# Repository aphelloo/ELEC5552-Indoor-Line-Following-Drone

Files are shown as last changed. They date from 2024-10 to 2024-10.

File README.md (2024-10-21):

# ELEC5552 Electrical Design Project Part 2 - Indoor Line Following Drone
<p align="center">
Project Overview
</p>

## Overview
The UWA Aviation Labs (UWAAL) consists of staff and students dedicated to developing advanced drone systems for various applications. UWAAL is currently working on an indoor drone system designed to perform autonomous remote safety inspections within the Australian National Fabrication Facility (ANFF) laboratories. Given the confined space and lack of GPS signal for navigation, the drone will be programmed to follow a predefined path marked by a line on the floor and hover at specific locations. Additionally, the drone will be equipped with obstacle avoidance capabilities to ensure safe and efficient operations during the inspection process.

## Repository Structure

| Section | Description |
| --- | --- |
| 3D CAD Design | For 3D Printed Shroud Design |
| Calculations | Calculations for component sizing |
| Code | Includes code-flow diagrams and programming files |
| Construction and Risks | Documentation on construction procedures and risk assessments associated with the project |
| Manual | Instructions for operation, safety and maintenance |
| Schematics | Schematics for drone, outlining the various connections |

## Required Applications
### On Laptop
* Betaflight Configurator
* Arduino IDE
* Raspberry Pi Imager
### On Phone
* Raspcontroller

## Acknowledgements
This project is made possible by contributions and feedback from the open-source hardware community, with support from ELEC5552 course staff and students.

## Licence
The CERN Open Hardware Licence Version 2 - Permissive (CERN-OHL-P) was chosen for its commitment to transparency and collaboration, allowing unrestricted use, modification, and distribution of the hardware designs and documentation. This license facilitates innovation and sharing within the community, ensuring that all adaptations and improvements remain openly accessible under the same terms. 

## Contributors
* Shraddha Domdala 
* Sharla Greyvenstein 
* Kate Miller 
* Ankona Pahari
* Anusree Rejukumar
* Thomas Robertson

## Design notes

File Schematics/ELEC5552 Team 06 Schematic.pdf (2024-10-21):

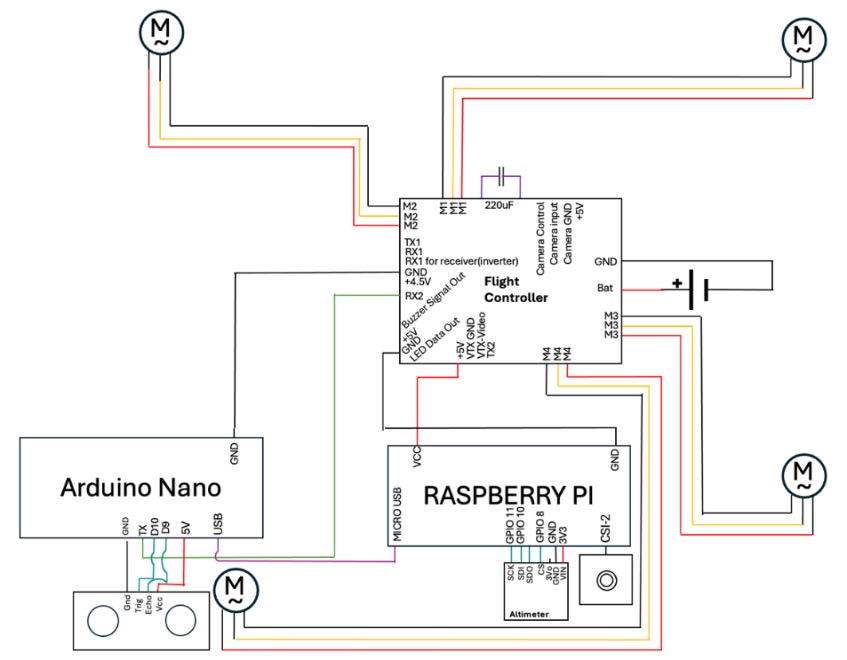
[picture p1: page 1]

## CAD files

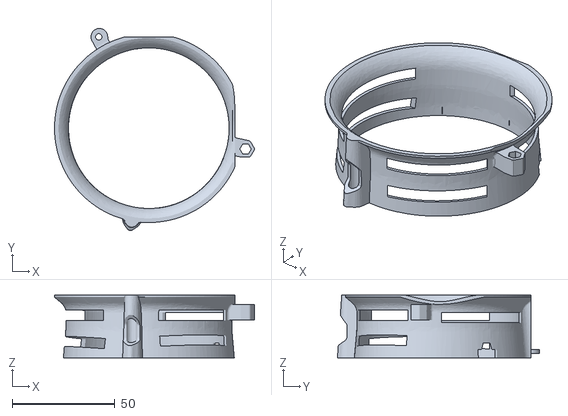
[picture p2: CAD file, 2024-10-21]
3D CAD Design/Front Right Shroud.stl
97.3 x 98.4 x 30.5

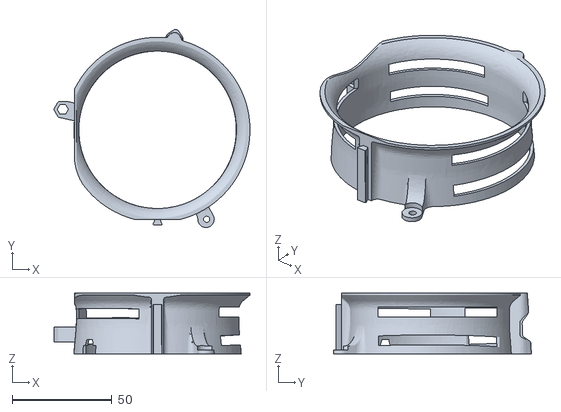
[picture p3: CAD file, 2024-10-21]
3D CAD Design/Rear Left Shroud.stl
98.3 x 99.3 x 30.5

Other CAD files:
3D CAD Design/Front Left Shroud.stl
3D CAD Design/Rear Right Shroud.stl

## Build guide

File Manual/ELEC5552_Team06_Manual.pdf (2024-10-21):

## Indoor Line Following Drone Project Team 06

Author(s)
Shraddha Domdala (23695285) Sharla Greyvenstein (22969519) Kate Miller (22965308)
Ankona Pahari (22903372)
Anusree Rejukumar (23943712) Thomas Robertson (23137408)

## Manual

## Volume 1

Project Partners: UWA Aviation Labs, Australian National Fabrication Facility (ANFF)

UWA Supervisor: John Dell

Team Number: 6

Group Meeting Day and Time: Tuesday 4pm

Word Count: 2258

### Version 2.0

## Revision History

Date | Version | Description | Author
10th September 2024 | 1.0 | Document has been initiated. | All
20th September 2024 | 2.0 | Edited Version | S. Greyvenstein

Contents Page

1. Safety

4
1.1 General Safety Warnings

4
1.2 Pre -Flight Safety Checklist

4
1.3 Operational Safety

4
1.4 Post Flight Safety

5
1.5 Emergency Action

5
1.6 Handling Hazardous Materials

5
1.7 Maintenance Safety

5

2. Operation

5
2.1 Required Prior to First Use

5
2.2 Operational Steps

6

3. Maintenance

7
3.1 Component Maintenance

7
3.2 Connection Maintenance

8

## Indoor Line-Following Drone Operation and Maintenance Manual

## 1. Safety

### 1.1 General Safety Warnings

- Prior to operating the drone, ensure you have thoroughly read and understood this manual. This will reduce the risks of accidents and potential harm to the user, bystanders, the surroundings, and the drone itself. Retain this manual for future reference.
- Indoor-use only: This drone has been designed, built, and coded for indoor operation. Use of the drone in an outdoor environment is beyond the specifications of this drone. Issues that may arise include but are not limited to; signal loss, unstable flight due to wind, dust, dirt, or moisture accumulation in components leading to potential malfunctions, overheating, or permanent damage.
- Avoid proximity to heat sources: Keep the drone away from heat sources as exposure to high temperatures can damage components or cause overheating.
- Avoid contact with water: Ensure the drone is kept away from water and other liquids. Exposure to moisture can lead to malfunctions and increase the risk of a crash.
- Do not touch operational drone: Whilst the drone is in flight, do not touch the under any circumstances
- 14+: This drone is intended for use by persons aged 14 years or older.
- Keep drone within sight: Do not allow drone to fly out of visible range.

### 1.2 Pre-Flight Safety Checklist

- Battery Inspection: Prior to each flight, inspect the drone battery. Ensure battery is fully charged and securely connected. Do not use a damaged, swollen, or leaking battery
- Component functionality tests: Run test codes for the flight controllers, microcontrollers, and sensors to confirm correct functionality.
- E-Stop operation validations: Verify the E-stop is functioning correctly and is accessible during flight. This enables immediate shutdown in the case of malfunction or unforeseen obstacles.
- Inspect motor windings: Verify that motor windings are clear of debris and appear undamaged.
- Inspect propellers: Verify that propellers are undamaged and that they are firmly attached to the motor shafts.

### 1.3 Operational Safety

- Ensure flight area is free from unnecessary bystanders: Avoid flying drone in area high crowded with bystanders.
- Maintain a safe distance from operational drone: Establish a safe distanced between the operator and bystanders, and the drone. Do not operate the drone near one’s face or eyes.

### 1.4 Post Flight Safety

- Safely turn off the drone: Upon flight completion (landed drone and stationary propellers) disconnect the battery.
- Damage inspection: After the drone has been safety depowered, inspect the drone for damage. Do not operate the drone if any part appears damaged or malfunctioning.
- Safe battery storage: Store the LiPo battery in an appropriately rated LiPo fireproof bag. Keep bag in a cool, dry location.
- Safe battery charging: Battery charging must be done under supervision and in a location out of reach of children. Allow battery to cool after use prior to charging. Do not charge a swollen or leaking battery.

### 1.5 Emergency Action

- Fire: If smoke or fire is present, do not handle the drone. Use a Carbon Dioxide Fire Extinguisher to extinguish flames.
- Crash response: In case of drone crash mid-flight, turn off the drone by disconnecting the battery prior to inspecting the drone for damage.

### 1.6 Handling Hazardous Materials

- Safe battery disposal: Do not dispose of the battery in curb side rubbish. Review your local disposal laws.
- Avoid contact with leaking battery: If battery leakage occurs, avoid contact with eyes or skin. If contact transpires, thoroughly wash exposed area with water and seek medical attention immediately.

### 1.7 Maintenance Safety

- Disconnect battery during maintenance: If maintenance works are to be performed on the drone, ensure battery is disconnected.
- Use proper tools: When changing or modifying drone parts, use only appropriate equipment and follow the manufacturer's instructions.

## 2. Operation

### 2.1 Required Prior to First Use

- Phone/Tablet with IOS or android access: To interact with the drone the user must download Raspcontroller, a free app which allows the user to remotely change GPIO pins.
- Stable Wi-Fi/Hotspot: To communicate with the Raspberry Pi, it must be connected to a local Wi-Fi
- MicroUSB Reader: In order for the Pi to operate in headless mode, the local Wi-Fi settings must be added to the bootup code. This is covered in Section 2.2.
- Line requirements: The line must be 8cm wide and be highly contrasting with the ground which itself cannot have complex patterns as this risks confusing the drone.

### 2.2 Operational Steps

1. Connecting to new Wi-Fi: For first use or when Wi-Fi settings have changed, complete the following steps.
a. Connect Raspberry Pi’s SD card into a SD card reader
b. Create a file called wpa_supplicant.conf
c. Put the following code into the wpa_supplicant.conf file. Ensure the County, SSID and PSK values are for your Wi-Fi settings.

country=AU
ctrl_interface=DIR=/var/run/wpa_supplicant GROUP=netdev update_config=1
network={
ssid="Your_SSID"
psk="Your_Password"
}
d. Insert SD Card into Raspberry Pi
2. Connect battery: The 2S battery must be firmly connected to the flight controller via the power cables located at the back of the drone. Care must be taken in ensuring the correct polarity is followed (black – black and red – red).
3. Ensure Power is reaching all components: Once the battery is connected, ensure the lights on the flight controller, Arduino, and Raspberry Pi have been activated. If there are any issues please refer to 1.d in Maintenance.
4. Wait for the Raspberry Pi light to stop flashing: Once the light has stopped flashing the Raspberry Pi has completed booting meaning the user will be able to connect. If this is the first time connecting the Raspberry Pi, please move to step 5 if not skip to step 6
5. First time Connection via Raspcontroller: In the Rasp controller app press the plus button. This will allow the user to enter information to be able to connect to the drone. Please enter the following values:
Device name: | drone
Host/IP Address: | drone.local
SSH Port: | 22
Timeout (sec): | 15
Username: | drone
Authentication: | Password
Password: | drone

Once these values have been entered press connection test.
6. Connection via Raspcontroller continued: Once connected this app can allow the user to check the camera, monitor CPU and RAM functionality, and remotely control the GPIO pins.
7. Connection via Raspcontroller continued – Remote GPIO: Once on GPIO control, the user must add GPIO5, GPIO19, GPIO21, GPIO26. Once enabled ensure they are all set to OUT and 0.
8. GPIO Functionality: The following commands are linked to GPIO pins:

GPIO5: | Arming Drone
GPIO19: | Hovering Mode
GPIO21: | Line Following Mode
GPIO26: | E-stop
9. Arming the Drone: The user must set GPIO5 to 1 to arm the drone – without this pin actived the drone will not function.
10. Launching the Drone: Following all safety instructions and keeping a safe distance away, setting GPIO19 to 1 will launch the drone to a stable height. When in this mode the drone will hover at a specific height and await further instructions.
11. Line Following: Setting GPIO21 to 1 will enable the line following mode. Ensure the drone is able to see the path through the check camera functionality on Raspcontroller. If no line is detected the drone will not leave hovering mode. Once line following has begun no more direct inputs are needed. For Line functionality, if the user requires the drone to stop at a particular place on the route, please use a perpendicular line. This will cause the drone to hold for 30s.
12. Emergency situations: If at any time the drone is operating in an unplanned manner that can be dangerous or if the drone needs to urgently stopped, set GPIO26 to 1. This will enable the drone’s failsafe mode causing it to land where it is.
13. Notes: Users should be aware that if the drone leaves Wi-Fi range for 30s the failsafe mode will also active.

## 3. Maintenance

### 3.1 Component Maintenance

a. Propeller: Propellers need to be regularly inspected before every flight to ensure that the propellers are not misshaped, discoloured, or fractured as these indicate that the propeller is worn/ old and needs replacement. Propellers should otherwise be replaced annually or after flying over 300 hours. Propellers should also be wiped down to clean off any foreign materials using a soft, dry cloth.
b. Motor: Motors should be regularly cleaned to remove dust and debris using a soft brush or cloth. A lubricant can be applied to the shaft and bearings to reduce noise and friction. Motor windings should be rotated by hand to check for blockages or rubbing prior to usage. Motor windings can also be inspected for any visual deformations. Do not do any powered testing of the motor if blockage, rubbing, or deformation is discovered. Instead, clean or replace where necessary. If not discovered, briefly power the motor and listen for any unusual sounds as these may indicate issues with the motor bearings. To extend motor longevity, avoid overloading as this puts additional strain on the motors.
c. Camera: Inspect the camera lense for any scratched, smudges, or foreign materials and ensure that the camera is firmly positioned before every flight. The camera lense can be wiped using a dust-free or microfibre cloth. If scratches are interfering with image-processing accuracy, camera replacement is necessary.
d. Battery: To guarantee optimal drone battery performance and longevity, inspect the battery on a regular basis for any physical damage, swelling, or leaks. If any of these are discovered, replace and dispose of the damaged battery safely according to local rules. Use a balance charger to equally charge all cells, preventing overcharging and extending battery life. Charge the battery to 50-60% capacity before storing it in a cool, dry location away from direct sunlight or harsh temperatures. If the battery is not in frequent use, cycle it every 1-2 months and avoid discharging it below 20% to prevent damage.
e. Frame: Inspect the frame on a regular basis for visible cracks, particularly after hard landings or crashes, and repair any damaged components to maintain structural integrity. Periodically check and tighten screws, especially those near motor mounts and frame connections, as vibrations can cause loosening over time. Clean the frame with compressed air or a soft brush to remove dirt, dust, and debris, paying special attention to vital places like motor mounts and gimbals to maintain smooth operation and avoid performance difficulties.
f. Frame arms: Inspect the frame arms on a regular basis for signs of warping, bending, or cracking, and replace any damaged arms as soon as possible. If weak areas or minor cracks emerge, consider strengthening them with epoxy or carbon fiber tape, however replacement is typically the best solution. Check that motor mounts are tightly attached, as loose screws might cause vibrations and performance concerns. Also, ensure that the propellers are balanced, since uneven propellers can put unnecessary strain on the frame arms, potentially causing damage over time.
g. Shrouds: As the shrouds are 3D printed, inspect them before and after each flight for cracks, deformation, or wear, especially following impacts. Clean them regularly to remove debris that could affect aerodynamics. Replace any damaged shrouds immediately using the same 3D print shroud layout to maintain consistency. When replacing, verify the size, and if needed, smooth the edges with sandpaper to ensure a proper fit. Store the drone in a dry, cool place to prevent unnecessary wear or pressure on the shrouds.

### 3.2 Connection Maintenance

a. Screw condition: Loose or worn screws can lead to mechanical failures or vibrations that reduce the drone’s overall performance. After every flight, inspect all screws for tightness, especially those securing the motors, and other moving parts. Vibration during flight can cause screws to loosen over time. Replace screws that show signs of wear, such as stripped threads or rust. Corrosion can compromise structural integrity and make it difficult to tighten or remove screws when necessary. When replacing screws, ensure they are not over-tightened, especially those securing the motors, as excessive force can damage the motor windings and compromise motor functionality. Apply thread locker solution (a mild one) to screws that are prone to loosening. This will ensure that they stay secure during flights while still being removable for maintenance.
b. Soldering condition: Soldered connections are crucial for maintaining electrical continuity in the power supply. Regularly inspect solder joints for cracks, cold joints, or oxidation, as weak points can lead to power loss or signal disruption. If any joint shows signs of wear, re-solder it immediately, taking proper precautions. When re-soldering, ensure no two connections are shorted and use a multimeter to verify continuity and detect any disconnections. Ensure cables and connectors are well-supported to avoid strain that could damage solder joints, especially those on the flight controller. During routine maintenance, handle the drone with care to prevent accidental pulling on these connections.
c. Cable condition: The condition of cables are crucial for power delivery and control signals. Ensure cables are neatly routed and secured with cable ties to prevent snagging and tangling, which can lead to disconnections or damage. Regularly inspect cables for fraying, exposed wires, or insulation damage, and replace any damaged cables immediately to avoid short circuits. Ensure that no wires cross the motor and propeller area to prevent cuts or entanglements, and handle the cable connection carefully especially the battery cable. Verify that all connectors are securely attached and free of corrosion or debris to maintain electrical continuity.

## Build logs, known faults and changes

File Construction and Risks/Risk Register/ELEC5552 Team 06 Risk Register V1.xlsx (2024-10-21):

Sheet: Risk Register
 | PROJECT RISK REGISTER
 | A risk is any factor, event or influence that threatens the successful completion of the project.
RISK DESCRIPTION |  | POTENTIAL IMPACT | RISK ASSESSMENT (Pre-mitigation) |  |  | RISK TREATMENT / MITIGATION | RISK ASSESSMENT (Post-mitigation) |  |  | RESPONSIBILITY
 |  |  | Consequence | Likelihood | Risk Rating- from risk matrix |  | Consequence | Likelihood | Risk Rating- from risk matrix
NO. | Project Scope
1 | Inadequate identification of in scope tasks | Not all aspects of scope was addressed in design | Major | Likely | E | Ask project partner clear technical clarifications | Major | Rare | M | All members- Identify TQs. Project Laison Manager- Submit TQs and attend info sessions.
2 | Inadequate identification of out of scope tasks | Time and effort put towards an aspect of the project that is irrelevant/ not under our control | Minor | Likely | H | Ask project partner clear technical clarifications | Minor | Unlikely | L | All members- Identify TQs. Project Laison Manager- Submit TQs and attend info sessions.
3 | Incorrect interpretation of scope | May inadvertantly go against a requirement | Major | Possible | E | Ask project partner clear technical clarifications in person when TQ response is received and a vague response is identified. Look at TQ responses from other groups. | Major | Rare | M | All members- Identify if response is unclear. Project Client Laison Manager - Raise questions to Project Partner.
4 | Scope creep | Change in scope was not identified or addressed, resulting in design proposed being based on out of date requirements | Moderate | Likely | H | Actively track requirements, updating when TQ responses are received and notifying all members if any changes to scope was made. | Moderate | Unlikely | M | Project Admin
 | Project Quality
5 | Project Team has limited experience with communication technologies | Limited knowledge means a lack of clarifty of complexity, impacting the quality of the design that can be delivered. | Minor | Possible | M | Research communication basics and components prior to starting design process | Minor | Unlikely | L | All members
6 | Project Team has limited experience with PCB design work | Limited capability to design PCBs impacts the quality of the design tha can be delivered. | Minor | Possible | M | Research PCB designs of revelant past projects to build knowledge of PCB design components. | Minor | Unlikely | L | All members
7 | Unclear level of quality demanded by project partner | May not deliver a design/ report that satisfies the expected standards quality | Minor | Possible | M | Be attentive to the rubrics of each area | Minor | Unlikely | L | All members
8 | Disagreements of individual expectation of quality | Members deliver sections with differing levels of quality, causing inconsistency in report flow or dissatisfaction among member regarding value of contribution | Minor | Likely | H | Check up with each individual's progress consistently to make sure disagreements/ dissatisfaction is not raise in the later half of the project | Minor | Unlikely | L | All members
9 | Being unable to find component meeting requirements | Unable to satisfy all requirements | Moderate | Possible | H | Be sure to look into multiple sources. If none is found meeting all requirements, pick a component that meets the essentials | Minor | Possible | M | All members
10 | Inadequate prioritising | May result in higher priority tasks being neglected, hence impacting their quality | Minor | Possible | M | Members must pay attention to rubric and course schedule to identify high priority tasks/ sections | Minor | Unlikely | L | All members
 | Project Schedule
11 | Unrealistic deadlines | Unrealistic deadlines may result in sections either being rushed and completed to a below-desired standard, or there being a knock on effect of tasks completed behind schedule | Moderate | Likely | H | Creation of a Gantt chart that allocates a realistic amount of time, accounting for how many tasks are expected to be completed concurrently and their priority | Minor | Possible | M | Project Controller
12 | Delay in prerequisite tasks | Delay in tasks that need to be completed before others can be started results in delay of progression of project | Moderate | Possible | H | Allocate enough members to complete prerequisite tasks to prevent delay | Minor | Unlikely | L | All members
13 | Unidentified tasks during schedule creation | Missed opportunity to do the tasks during the optimal time, causing delay in progression of project | Minor | Possible | M | Disect all rubrics and guides to identify what components are expected to be covered | Minor | Unlikely | L | All members
14 | Higher external priorities | Members having higher external may mean some individuals become unavailable at inopportune times, causing delay in their contribution or communication | Moderate | Likely | H | All members must give warning if they foresee a period of time during which they will be unavailable. Members must complete their contribution prior to becoming unavailable. | Minor | Possible | M | All members
15 | Change in submission dates | Reduces time in which project can be completed, resulting in requirement to review project schedule to prevent missing submission date | Moderate | Rare | M | All members must regularly attend to updates made on LMS or during lecture/ info sessions and notify other members. Gantt chart should also be designed such that tasks are completed prior to the submission dates. | Minor | Rare | L | All members - Check LMS, lectures, info session announcements Project Controller- Create optimistic Gantt chart
16 | Conflicting idea proposal | Conflicting idea proposals require member to spend more time to investigate each option to determine best option | Minor | Possible | M | Members making proposals should already have facts backing their proposal to allow other members to come to the decision without requiring more research, hence time. | Insignificant | Possible | L | All members
17 | Delayed TQ reponses | May delay ability to move on to next tasks/ make informed decisions | Minor | Likely | H | Identify tasks that can be worked on without the most up to date information. | Insignificant | Likely | M | All members
18 | Missed TQ submission deadline | Delays ability to move on to next tasks/ make informed decisions as clarification questions are unable to be answered until next info session | Moderate | Possible | H | All members must upload their TQs to the register a day prior to the submission date. TQ submissions must be done the night before the submission date. Upcoming submission dates will be raised. | Moderate | Unlikely | M | All members - Upload TQs Project Controller- Remind Project Client Laison Manager of submission deadline. Project Client Laison Manager: Submit TQs prior to deadline.
19 | Missed information session | Delays ability to move on to next tasks/ make informed decisions as clarification questions are unable to be answered until next TQ submission date | Minor | Possible | M | Discuss among member such that at least one member must attend the session live. TQ submission should also be comprehensive such that only clarification of TQs are needed. | Minor | Rare | L | All members
20 | Mental stress | Stress may incur over the course of the project, resulting in members getting overwhelmed and unable to work efficiently, slowing down progress | Minor | Likely | H | Create a Gantt chart that allocates adequate time and allocate tasks to prevent overloadin a particular individual. | Minor | Unlikely | L | All members
21 | Poor design | May result in requirement to redesign, meaning more time spent on research and report rewrite and re-running simulations. | Major | Possible | E | All members must throroughly research their topic. Raise TQs if clarification is required. | Moderate | Unlikely | M | All members
22 | Missed submission date | Unable to complete all tasks to meet project deadline, resulting in lost marks every day it's late | Moderate | Possible | H | All members must be aware of course schedule. Upcoming submission dates will be raised. | Moderate | Unlikely | M | All members- Be aware of course schedule. Project Controller- Remind members of upcoming submission dates.
 | Project Cost
23 | Project is over budget | Project components may be overbudget as a result of meeting requirements, resulting in exceeding the budget limit | Moderate | Possible | H | Select components by taking cost into account. | Moderate | Unlikely | M | All members
24 | Lack of local resources | Lack of local resources means reliance on imported goods, raising risks of being overbudget as there are import/ shipping fees and currency conversion. | Minor | Likely | H | Ask other groups about sources (not specific components) | Minor | Unlikely | L | All members
25 | Lack of access to open-source resources for simulation/ modelling | Lack of open-source resources means reliance on resources that require obtaining a license and paying fees | Minor | Possible | M | Enquire into possible resources through TQs. | Minor | Unlikely | L | All members
 | Project Stakeholders
26 | Lack of communication management | Lack of communication management could damage relationship with stakeholder, reducing their willingness to contribute/ collaborate. | Moderate | Possible | H | Be clear and concise when asking clarifications (making sure questions are relevant) from Project Partner. | Minor | Unlikely | L | All members.
27 | Lack of communication among project team | Confusion about task allocations, deadline and/or design hinders effective completion of design project | Moderate | Possible | H | Be clear and concise when allocating tasks and merging individual contributions. | Minor | Possible | M | All members
28 | Unidentified stakeholder | Stakeholder's requirements are unaddressed | Moderate | Possible | H | Ask Dilusha clarification questions about specific stakeholders | Minor | Unlikely | L | All members
29 | Unclear role of stakeholder | Unclear identification of how stakeholder affects project may deterriorate relationship with them as they are not properly handled | Minor | Possible | M | Ask Dilusha clarification questions about specific stakeholders | Minor | Unlikely | L | All members
30 | Lack of integration of feedback | Feedback is not address in design, leading to neglecting the stakeholder. | Moderate | Possible | H | Regularly attend to the registries and notify members if changes were made. | Moderate | Unlikely | M | All members
 | Risks in Design
31 | Propeller interference | Propeller coming in contact with objects, causing damage or potentially breakage of the propeller. | Major | Likely | E | Propeller guards of shrouds to protect the propellers | Major | Unlikely | M | All members, end users
32 | Component Failure | Components in the drone (motors, propellers, battery, sensors, flight controller, ESC, communication modules, MCUs, or power distribution system) could fail due to mechanical stress, overheating, electrical faults, or poor handling. | Major | Likely | E | Regular maintenance and inspections should be performed on all critical parts to detect wear and potential issues early. | Moderate | Unlikely | M | All members, end users
33 | Communication Loss | There could be communication delays or loss of signal between the Raspberry Pi and the Arduino Nano, causing delays in executing commands. Communication loss may also interfere with E-stop functionality. | Moderate | Possible | H | Use reliable communication protocols and include error-checking mechanisms to ensure commands are executed properly. | Minor | Unlikely | L | All members, end users
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

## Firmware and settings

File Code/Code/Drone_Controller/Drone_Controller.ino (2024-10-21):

#include "global.h"
#include "SER.h"
//Choose either pin 2 or pin 3 because they are interrupt pins. On other boards you can use any pin that has an interrupt
#define OUTPUT_PIN 3 
#define RC_CHANNEL_MIN 990
#define RC_CHANNEL_MAX 2010

#define SBUS_MIN_OFFSET 173
#define SBUS_MID_OFFSET 992
#define SBUS_MAX_OFFSET 1811
#define SBUS_CHANNEL_NUMBER 16
#define SBUS_PACKET_LENGTH 25
#define SBUS_FRAME_HEADER 0x0f
#define SBUS_FRAME_FOOTER 0x00
#define SBUS_FRAME_FOOTER_V2 0x04
#define SBUS_STATE_FAILSAFE 0x08
#define SBUS_STATE_SIGNALLOSS 0x04
#define SBUS_UPDATE_RATE 15 //ms
int ch0 = 1500 , ch1 = 1500 , ch2 = 900, ch3 =1500, ch4 = 900, ch5 = 900, ch6 = 900;
long duration, distance;
int EchoMid = 9; // Ultrasonic sensor Echo pin
int TrigMid = 10;  // Ultrasonic sensor Trigger pin
void sbusPreparePacket(uint8_t packet[], int channels[], bool isSignalLoss, bool isFailsafe){

    static int output[SBUS_CHANNEL_NUMBER] = {0};

    /*
     * Map 1000-2000 with middle at 1500 chanel values to
     * 173-1811 with middle at 992 S.BUS protocol requires
     */
    for (uint8_t i = 0; i < SBUS_CHANNEL_NUMBER; i++) {
        output[i] = map(channels[i], RC_CHANNEL_MIN, RC_CHANNEL_MAX, SBUS_MIN_OFFSET, SBUS_MAX_OFFSET);
    }

    uint8_t stateByte = 0x00;
    if (isSignalLoss) {
        stateByte |= SBUS_STATE_SIGNALLOSS;
    }
    if (isFailsafe) {
        stateByte |= SBUS_STATE_FAILSAFE;
    }
    packet[0] = SBUS_FRAME_HEADER; //Header

    packet[1] = (uint8_t) (output[0] & 0x07FF);
    packet[2] = (uint8_t) ((output[0] & 0x07FF)>>8 | (output[1] & 0x07FF)<<3);
    packet[3] = (uint8_t) ((output[1] & 0x07FF)>>5 | (output[2] & 0x07FF)<<6);
    packet[4] = (uint8_t) ((output[2] & 0x07FF)>>2);
    packet[5] = (uint8_t) ((output[2] & 0x07FF)>>10 | (output[3] & 0x07FF)<<1);
    packet[6] = (uint8_t) ((output[3] & 0x07FF)>>7 | (output[4] & 0x07FF)<<4);
    packet[7] = (uint8_t) ((output[4] & 0x07FF)>>4 | (output[5] & 0x07FF)<<7);
    packet[8] = (uint8_t) ((output[5] & 0x07FF)>>1);
    packet[9] = (uint8_t) ((output[5] & 0x07FF)>>9 | (output[6] & 0x07FF)<<2);
    packet[10] = (uint8_t) ((output[6] & 0x07FF)>>6 | (output[7] & 0x07FF)<<5);
    packet[11] = (uint8_t) ((output[7] & 0x07FF)>>3);
    packet[12] = (uint8_t) ((output[8] & 0x07FF));
    packet[13] = (uint8_t) ((output[8] & 0x07FF)>>8 | (output[9] & 0x07FF)<<3);
    packet[14] = (uint8_t) ((output[9] & 0x07FF)>>5 | (output[10] & 0x07FF)<<6);  
    packet[15] = (uint8_t) ((output[10] & 0x07FF)>>2);
    packet[16] = (uint8_t) ((output[10] & 0x07FF)>>10 | (output[11] & 0x07FF)<<1);
    packet[17] = (uint8_t) ((output[11] & 0x07FF)>>7 | (output[12] & 0x07FF)<<4);
    packet[18] = (uint8_t) ((output[12] & 0x07FF)>>4 | (output[13] & 0x07FF)<<7);
    packet[19] = (uint8_t) ((output[13] & 0x07FF)>>1);
    packet[20] = (uint8_t) ((output[13] & 0x07FF)>>9 | (output[14] & 0x07FF)<<2);
    packet[21] = (uint8_t) ((output[14] & 0x07FF)>>6 | (output[15] & 0x07FF)<<5);
    packet[22] = (uint8_t) ((output[15] & 0x07FF)>>3);

    packet[23] = stateByte; //Flags byte
    packet[24] = SBUS_FRAME_FOOTER; //Footer
}

uint8_t sbusPacket[SBUS_PACKET_LENGTH];
int rcChannels[SBUS_CHANNEL_NUMBER];
uint32_t sbusTime = 0;



void setup() {
    rcChannels[0] = 1500;// Roll
    rcChannels[1] = 1500;// Pitch
    rcChannels[2] = 900; //Throttle
    rcChannels[3] = 1500; // Yaw
    rcChannels[4] = 900; // Aux1
    rcChannels[5] = 900; // Aux2
    rcChannels[6] = 900; // Aux2
    Serial.begin(100000, SERIAL_8E2);
    pinMode(TrigMid, OUTPUT);
    pinMode(EchoMid, INPUT);
}

void loop() {
    uint32_t currentMillis = millis();
      ser.begin();
      
      digitalWrite(TrigMid, 0);
      delayMicroseconds(2);   
      digitalWrite(TrigMid, 1);  // Send ultrasonic pulse
      delayMicroseconds(10);
      digitalWrite(TrigMid, 0);

      duration = pulseIn(EchoMid, 1); // Receive reflected pulse
      distance = duration * 0.034 / 2;   // Convert to distance in cm
    if(distance <100 ) { 
      rcChannels[0] = 1500;// Roll
      rcChannels[1] = 1500;// Pitch
      rcChannels[2] = 1500; //Throttle
      rcChannels[3] = 1500; // Yaw
      rcChannels[4] = 1850; // Aux1
      rcChannels[5] = 1100; // Aux2
      rcChannels[6] = 2000; // OB
    }
    else {
      rcChannels[0] = ch0;// Roll
      rcChannels[1] = ch1;// Pitch
      rcChannels[2] = ch2; //Throttle
      rcChannels[3] = ch3; // Yaw
      rcChannels[4] = ch4; // Aux1
      rcChannels[5] = ch5; // Aux2
      rcChannels[6] = 1000; // OB
    }
    if (currentMillis > sbusTime) {
        sbusPreparePacket(sbusPacket, rcChannels, false, false);
        Serial.write(sbusPacket, SBUS_PACKET_LENGTH);

        sbusTime = currentMillis + SBUS_UPDATE_RATE;
    }

     
      
      // If an obstacle is detected within 25 cm, stop the drone
      if (distance < 100) {
        Serial.println("Obstacle detected!");
      // delay(10);
      // hover(); 
      } else {
        Serial.println("Continue ");
      }
}

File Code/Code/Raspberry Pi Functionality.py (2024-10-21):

from picamera2 import Picamera2, Preview
import time
import cv2
import numpy as np
import serial
import RPi.GPIO as GPIO
#set up serial communication
ser = serial.Serial('dev/ttyUSB0',baudrate = 100000, bitsize = serial.EIGHTBITS, parity=serial.PARITY_EVEN, stopbits=serial.STOPBITS_TWO,timeout=1)
#GPIO Setup
pins = [5, 19, 21, 26]
for pin in pins:
    GPIO.setup(pin, GPIO.OUT)

for pin in pins:
    GPIO.output(pin, GPIO.LOW)
#Element Decleration
cap_matrix = np.zeros((3,3))
intensity_values = []
threshold = 128
high = 0
chosen_M = []
Commands =[]
Direction =""
#activate picam2
picam2 = Picamera2()
camera_config = picam2.create_preview_configuration()
picam2.configure(camera_config)
picam2.start()
#List of Active Matrix's
M1 = np.array([[1, 1, 1],
               [1, 1, 1],
               [1, 1, 1]])
#Straight
M2 = np.array([[ 1,  1,  1],
               [ 1,  1,  1],
               [ 1,  1, -1]])
#slow right
M3 = np.array([[ 1,  1,  1],
               [ 1,  1,  1],
               [ 1, -1, -1]])
#Hard Right
M4 = np.array([[ 1,  1,  1],
               [ 1,  1,  1],
               [-1,  1,  1]])
#Slow Left
M5 = np.array([[ 1,  1,  1],
              [ 1,  1,  1],
              [-1,  1, -1]])
#Slow Down - Could be perp Line
M6 = np.array([[ 1,  1,  1],
               [ 1,  1,  1],
               [-1, -1,  1]])
#Hard Right
M7 = np.array([[ 1,  1,  1],
               [ 1,  1,  1],
               [-1, -1, -1]])
#Forward
M8 = np.array([[ 1,  1,  1],
                [ 1,  1, -1],
                [ 1,  1, -1]])
#Sharp Right
M9 = np.array([[ 1,  1,  1],
                [ 1,  1, -1],
                [ 1, -1, -1]])
#Right
M10 = np.array([[ 1,  1,  1],
                [ 1, -1, -1],
                [ 1, -1, -1]])
#Sharp Right
M11 = np.array([[ 1,  1,  1],
                [-1,  1,  1],
                [-1,  1,  1]])
#Sharp Left
M12 = np.array([[ 1,  1,  1],
                [-1,  1, -1],
                [-1,  1, -1]])
#Forward
M13 = np.array([[ 1,  1,  1],
                [-1, -1,  1],
                [-1, -1,  1]])
#slow Left
M14 = np.array([[ 1,  1,  1],
                [-1, -1, -1],
                [-1, -1, -1]])
#forward
M15 = np.array([[ 1,  1, -1],
                [ 1,  1, -1],
                [ 1,  1, -1]])
#left
M16 = np.array([[ 1,  1, -1],
                [ 1, -1, -1],
                [-1, -1, -1]])
#slow right
M17 = np.array([[ 1,  1, -1],
                 [-1,  1, -1],
                 [ 1,  1,  1]])
#forward
M18 = np.array([[ 1,  1, -1],
                 [-1,  1, -1],
                 [-1,  1, -1]])
#forward (slight left)
M19 = np.array([[ 1, -1, -1],
                 [ 1, -1, -1],
                 [ 1, -1, -1]])
#Move to Right
M20 = np.array([[-1,  1,  1],
                 [-1,  1,  1],
                 [-1,  1,  1]])
#Right
M21 = np.array([[-1,  1, -1],
                 [ 1,  1,  1],
                 [-1,  1, -1]])
#Pause - 30 seconds
M22 = np.array([[-1, -1, -1],
                 [ 1,  1,  1],
                 [ 1,  1,  1]])
#forward
M23 = np.array([[-1, -1, -1],
                 [ 1,  1, -1],
                 [ 1,  1, -1]])
#sharp Left
M24 = np.array([[-1, -1, -1],
                 [-1,  1,  1],
                 [-1,  1,  1]])
#Sharp Right
M25 = np.array([[-1, -1, -1],
                 [-1, -1, -1],
                 [ 1,  1,  1]])
#forward
M26 = np.array([[-1, -1, -1],
                 [-1, -1, -1],
                 [-1, -1, -1]])
#stationary

Collection = [M1,M2,M3,M4,M5,M6,M7,M8,M9,M10,M11,M12,M13,M14,M15,M16,M17,M18,M19,M20,M21,M22,M23,M24,M25,M26]
#Image Processing tool

while True:
    #Image Processing
    frame = picam2.capture_array()
    cv2.GaussianBlur(frame, (5,5), 0)
    roi = frame[0:480,0:640]
    gray = cv2.cvtColor(roi, cv2.COLOR_BGR2GRAY)
    _, BI = cv2.threshold(gray, 127, 255, cv2.THRESH_BINARY)
    #seperating into [3x3] matrix images
    TL = BI[0:int(320/3), 0:int(320/3)]
    TM = BI[0:int(320/3), int(320/3):int(320/3)*2]
    TR = BI[0:int(320/3), 2*int(320/3):320]
    ML = BI[int(320/3):int(320/3)*2, 0:int(320/3)]
    MM = BI[int(320/3):int(320/3)*2, int(320/3):int(320/3)*2]
    MR = BI[int(320/3):int(320/3)*2, 2*int(320/3):320]
    BL = BI[int(320/3)*2:320, 0:int(320/3)]
    BM = BI[int(320/3)*2:320, int(320/3):int(320/3)*2]
    BR = BI[int(320/3)*2:320, 2*int(320/3):320]
    regions = [TL,TM,TR,ML,MM,MR,BL,BM,BR]
    #mean thresholding into -1/1
    for i in regions:
        intensity = np.mean(i)
        if intensity < threshold:
            intensity_values.append(-1)
        else:
            intensity_values.append(1)
    #make values into matrix
    id_matrix = np.array(intensity_values).reshape((3,3))
    #matrix comparison process
    for i in Collection:
        if high < np.sum(id_matrix*i):
            chosen_M = i
            high = np.sum(id_matrix*i)
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

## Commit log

2024-07-30 Create 3D CAD Design
2024-10-21 Added 3d shroud design
    [Front Left Shroud.stl, Front Right Shroud.stl, Rear Left Shroud.stl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]
